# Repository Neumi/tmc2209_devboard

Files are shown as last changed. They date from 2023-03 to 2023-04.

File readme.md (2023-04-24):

# TMC2209 Development Board for Arduino Uno
A development board to test the Trinamic TMC2209 stepper motor controller on an Arduino Uno.

This board should cover all options and IOs that Trinamic provides for its TMC2209.

Facts:
 - All TMC2209 pins are connected to digital pins of the Arduino. 
 - XT30 power connector
 - voltage source selector Arduino VIN or XT30
 - TVS diodes on 5v and 28V lane of the TMC2209
 - different wiring schemes for the JST motor connector (because getting the right phases is not easy apparently!)
 - different current setting selectable with solder bridges (or custom resistor also possible)
 - motor voltage sensing via voltage divider on A0
 - reset button for Arudino + power LED

KICAD and production files for JLCPCB are also included. Code will follow. 
Production cost incl assembly is around 50€ for 5pcs. THT components not included.

Feedback is very welcome!

## Video:
LINK TO VIDEO (https://www.youtube.com/watch?v=-AFWAARrtoE)

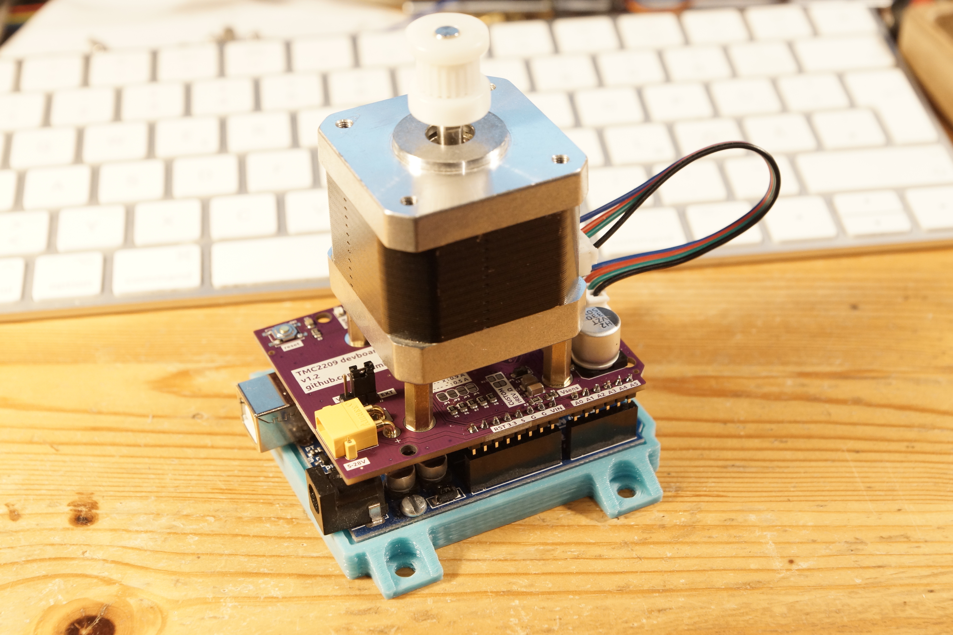
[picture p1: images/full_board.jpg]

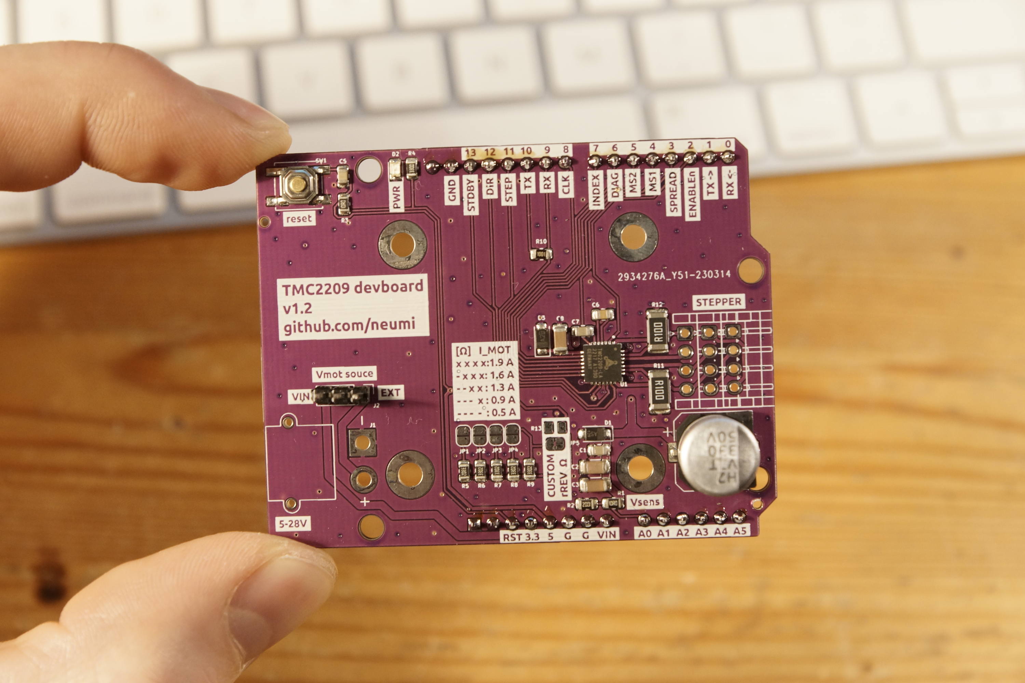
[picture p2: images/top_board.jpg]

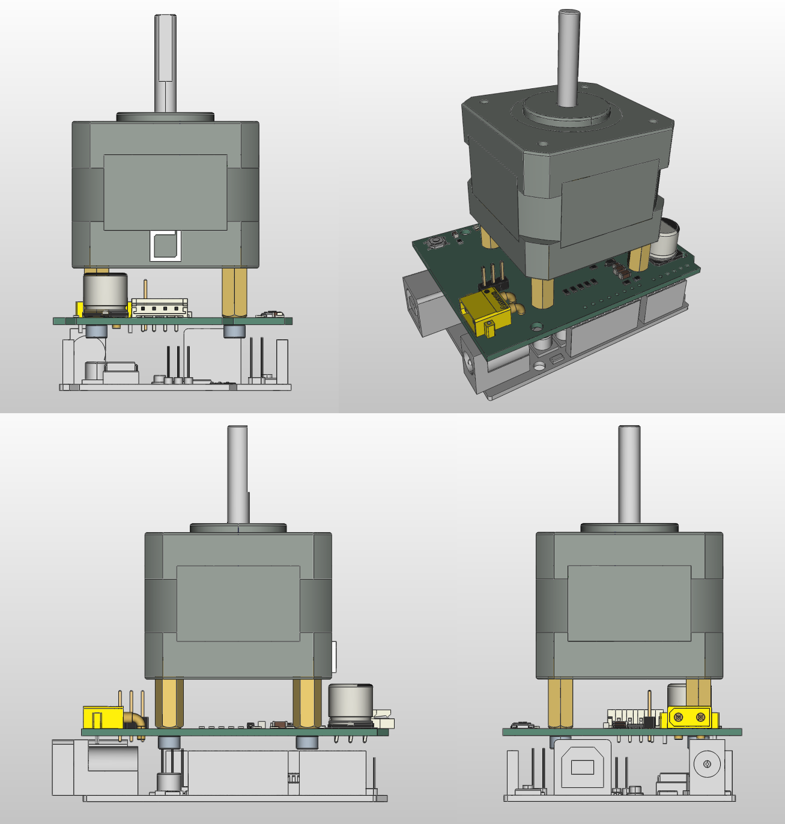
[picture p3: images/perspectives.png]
PCB assembly perspectives

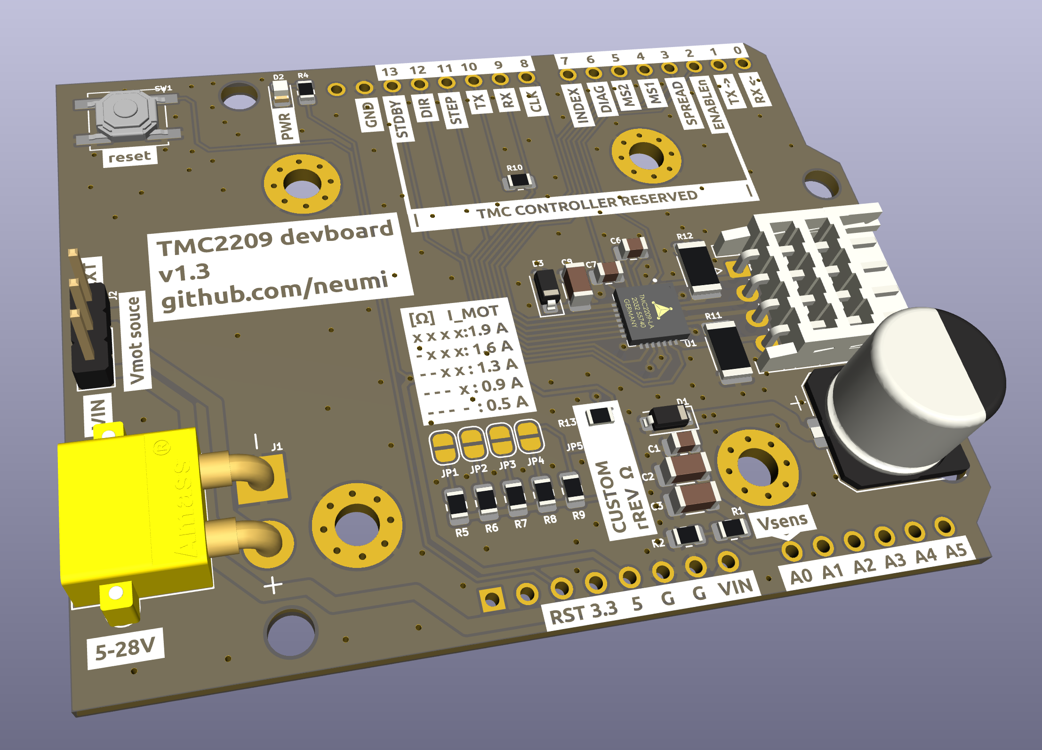
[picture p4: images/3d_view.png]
PCB 3d view

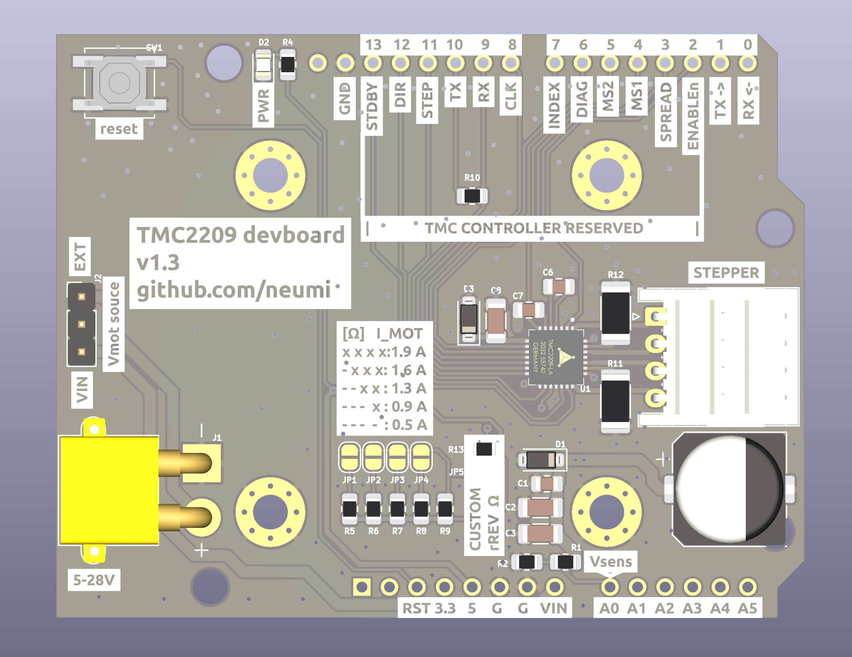
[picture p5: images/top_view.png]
top view

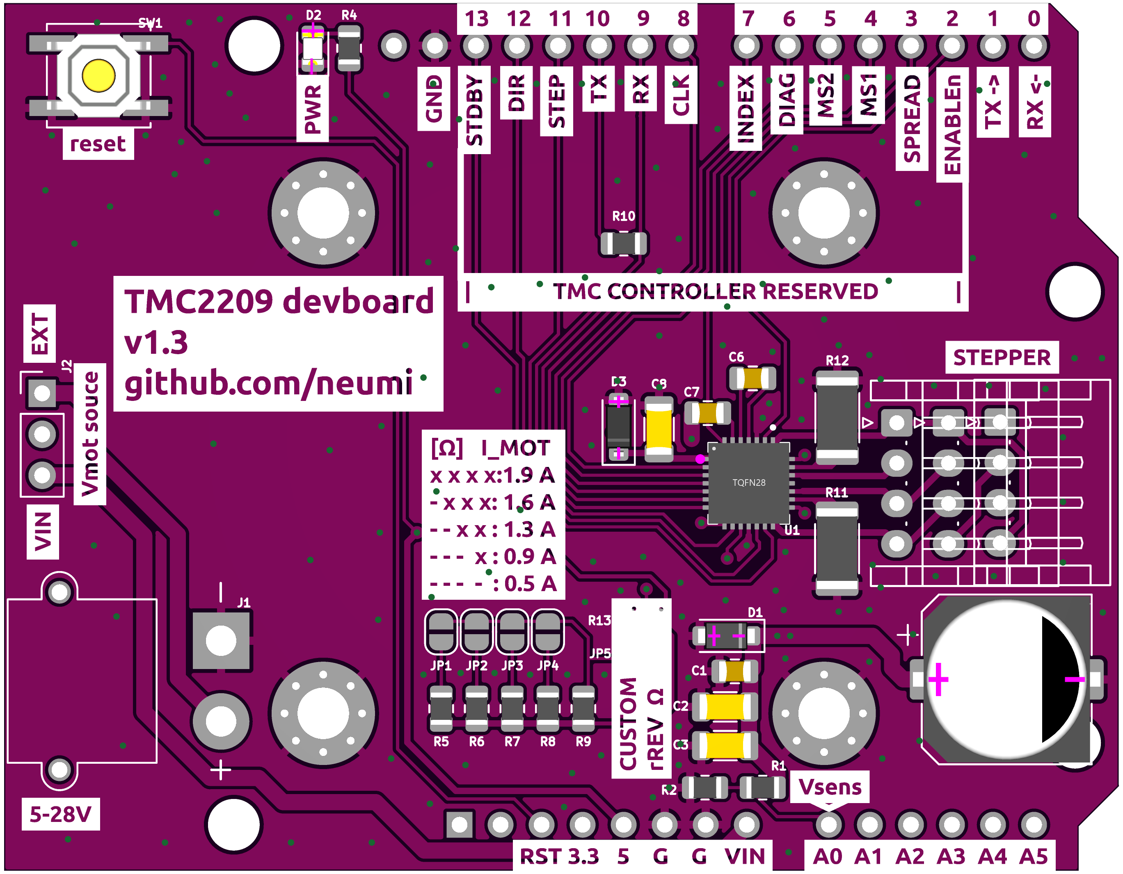
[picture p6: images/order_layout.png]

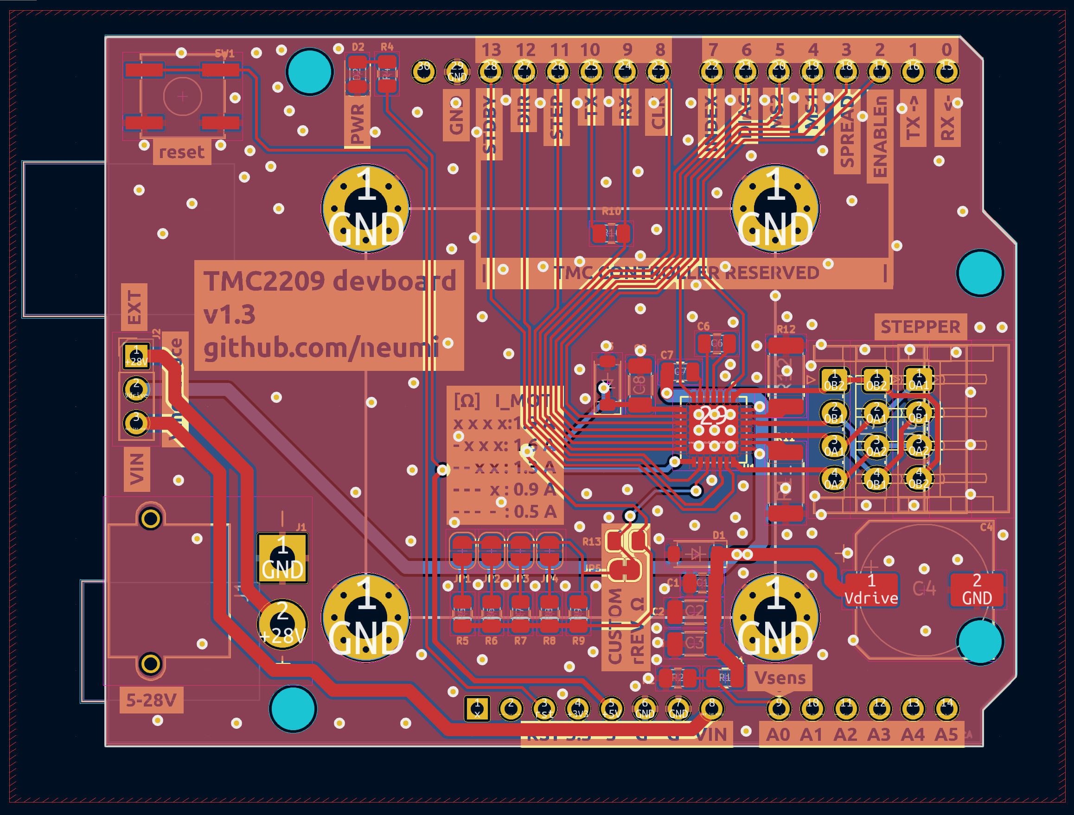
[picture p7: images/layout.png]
PCB layout


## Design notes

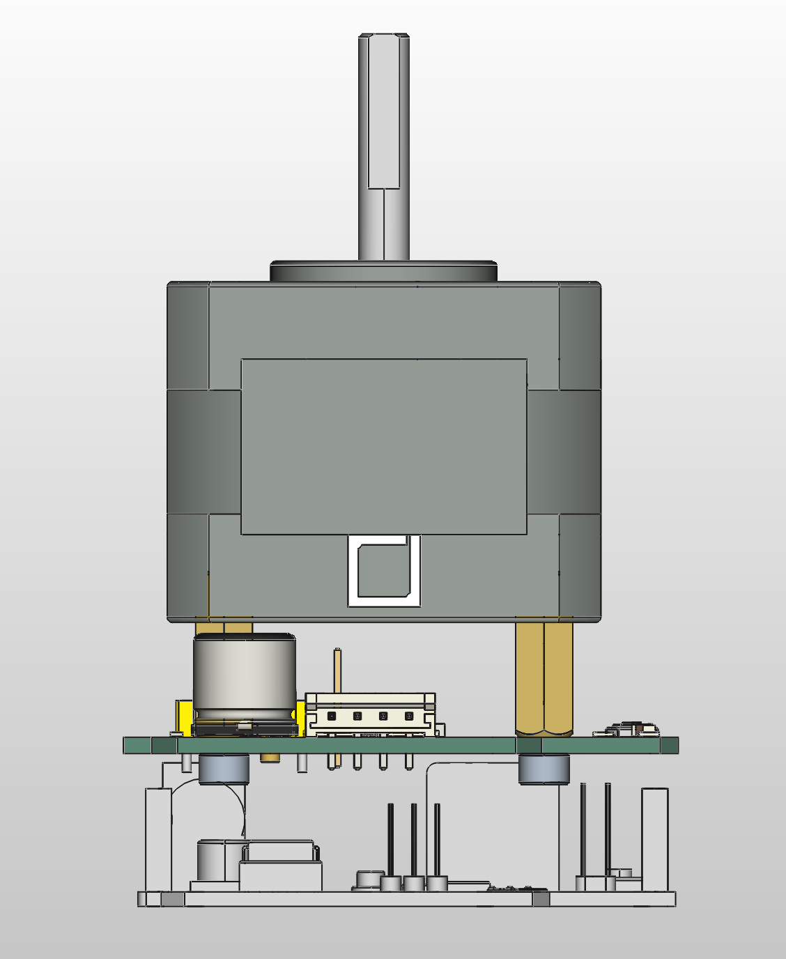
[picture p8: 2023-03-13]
images/back.png

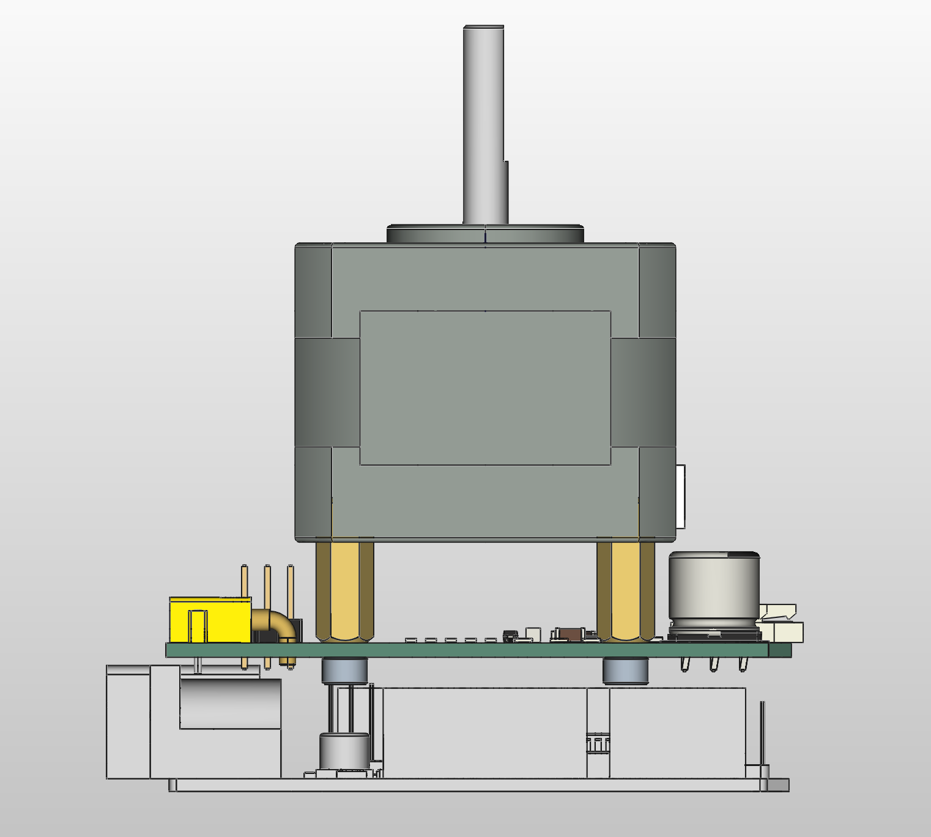
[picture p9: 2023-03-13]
images/side.png

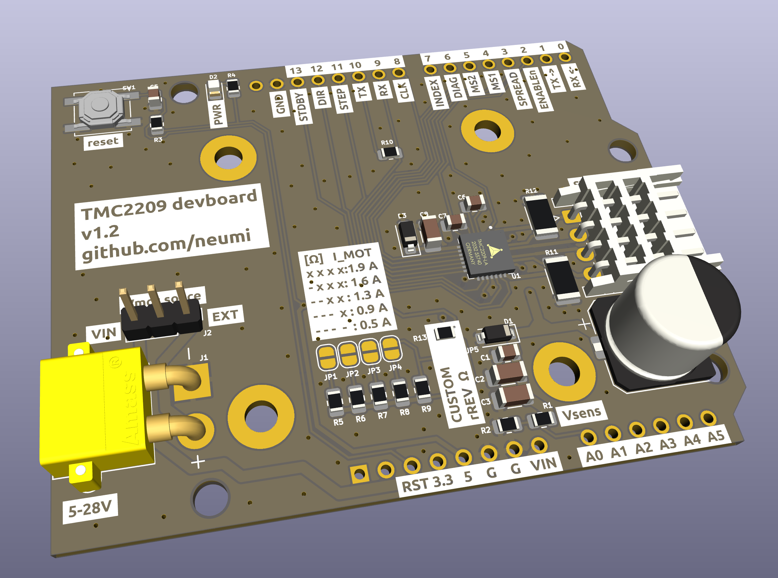
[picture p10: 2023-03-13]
images/3d _view.png

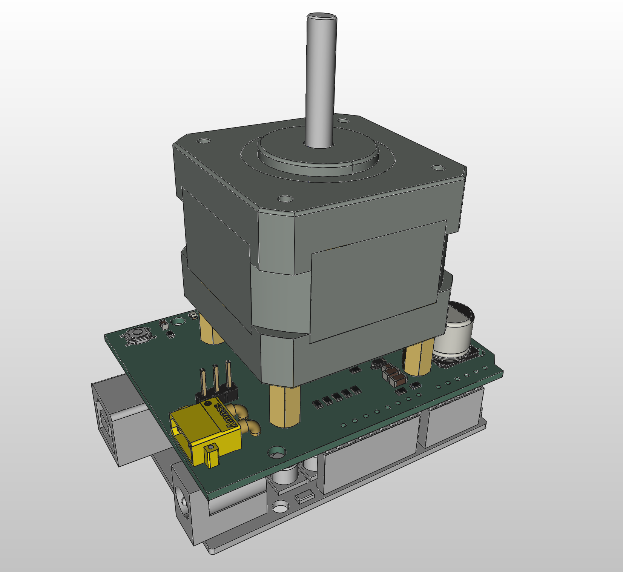
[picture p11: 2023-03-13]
images/diagonal.png

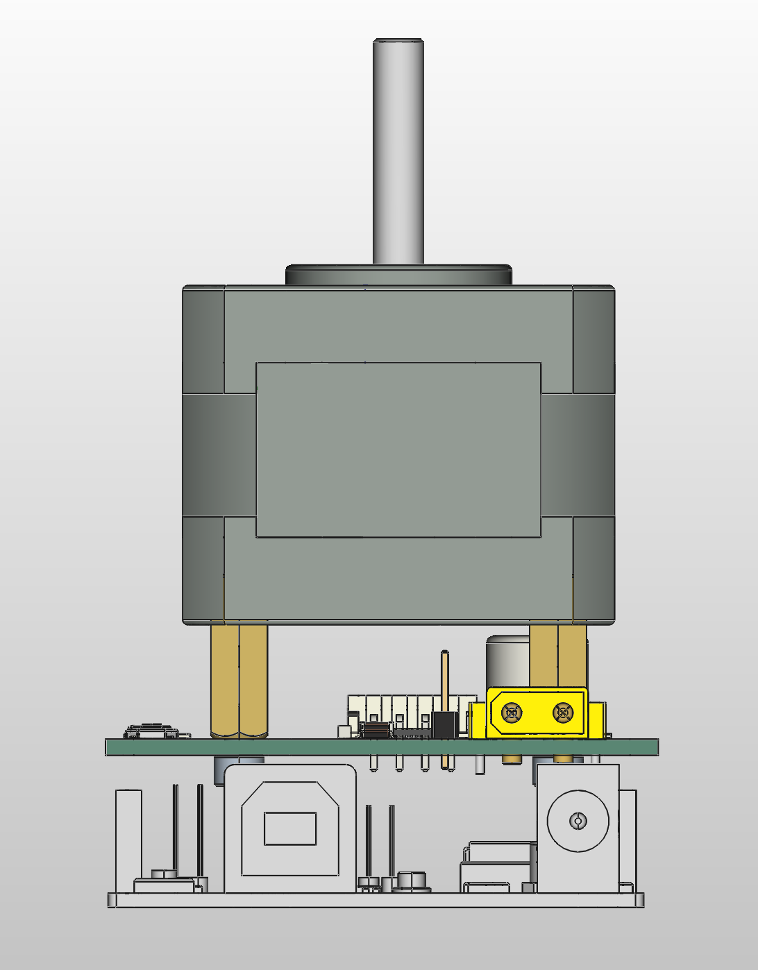
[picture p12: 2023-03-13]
images/front.png

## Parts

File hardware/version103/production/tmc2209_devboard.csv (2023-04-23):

Comment | Designator | Footprint | LCSC
C100nF | C1,C7 | Capacitor_SMD:C_0805_2012Metric | C49678
C10uF | C2 | Capacitor_SMD:C_1206_3216Metric | C13585
C4.7uF | C3 | Capacitor_SMD:C_1206_3216Metric | C29823
C_330uF | C4 | Capacitor_SMD:CP_Elec_10x10 | C249985
C22nF 50V | C6 | Capacitor_SMD:C_0805_2012Metric | C1729
C2.2-4.7uF ceramic | C8 | Capacitor_SMD:C_1206_3216Metric | C29823
D_TVS_30V | D1 | Diode_SMD:D_SOD-123 | C553410
LED | D2 | LED_SMD:LED_0805_2012Metric | C84256
D_TVS_5V | D3 | Diode_SMD:D_SOD-123 | C478011
Conn_01x03_Pin | J2 | Connector_PinHeader_2.54mm:PinHeader_1x03_P2.54mm_Vertical
motor_conn | J4,J5,J6 | Connector_JST:JST_EH_S4B-EH_1x04_P2.50mm_Horizontal
Jumper | JP1,JP2,JP3,JP4 | Jumper:SolderJumper-2_P1.3mm_Open_RoundedPad1.0x1.5mm
SolderJumper_2_Bridged | JP5 | Jumper:SolderJumper-2_P1.3mm_Bridged_RoundedPad1.0x1.5mm
R10k | R1 | Resistor_SMD:R_0805_2012Metric | C3016734
R1k | R10 | Resistor_SMD:R_0805_2012Metric | C17513
R100mOHM | R11,R12 | Resistor_SMD:R_2010_5025Metric | C175979
R2k | R2 | Resistor_SMD:R_0805_2012Metric | C17604
R330 | R4 | Resistor_SMD:R_0805_2012Metric | C17630
R33k | R5,R6,R7,R8,R9,R13 | Resistor_SMD:R_0805_2012Metric | C17633
SW_Push | SW1 | Button_Switch_SMD:SW_Push_1P1T_NO_CK_KSC6xxJ | C318884
TMC2209-LA | U1 | components:QFN50P500X500X90-29N | C465949

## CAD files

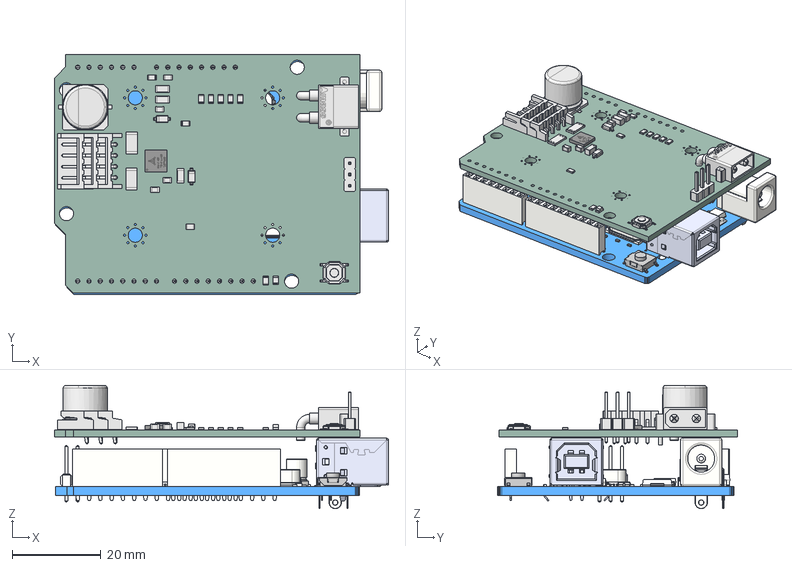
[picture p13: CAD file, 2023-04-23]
hardware/version103/tmc2209_devboard_assembly_103.FCStd
75.4 x 54.1 x 27.8 mm
PCB
pcb
16MHz Crystal
16MHz Crystal001
DC_Jack
heder female 8
heder female 009
heder female 10
red buttom
header male 2
header male 003
header male 004
heder female 6
47uF 27v cap
47uF 27v cap001
Atmega328p-AU
LM358
CH340G
LM1117
transistor SOC
transistor SOC001
diode
R1
0603 Package
0603 Package001
0603 Package002
0603 Package003
0603 Package004
0603 Package005
0603 Package006
0603 Package007
0603 Package008
0603 Package009
0603 Package010
0603 Package011
0603 Package012
0603 Package013
0603 Package014
0603 Package015
0603 Package016
0603 Package017
0603 Package018
0603 Package019
0603 Package020
0603 Package021

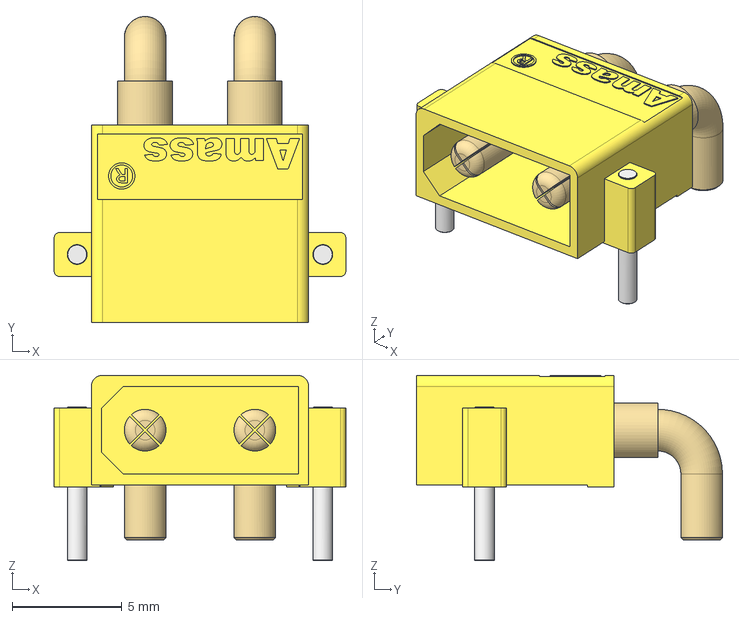
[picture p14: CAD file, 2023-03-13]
hardware/version103/3d_files/XT30PW-M_pcb.stp
13.3 x 13.9 x 8.45 mm

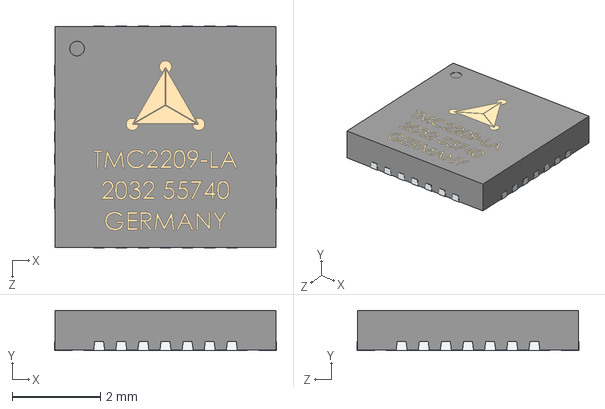
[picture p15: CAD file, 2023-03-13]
hardware/version103/3d_files/TMC2209.STEP
5.02 x 0.911 x 5.02 mm

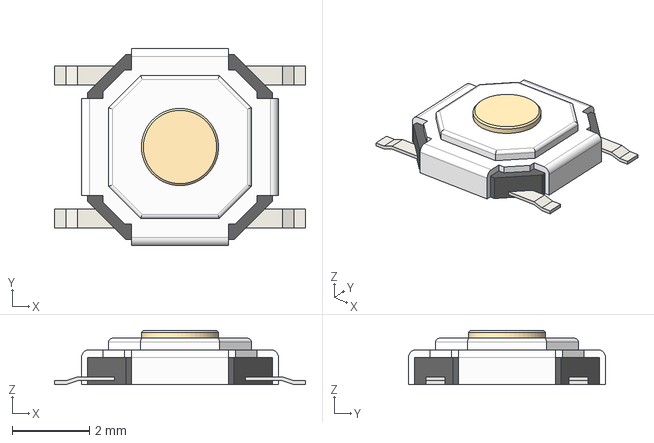
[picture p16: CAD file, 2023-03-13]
hardware/version103/3d_files/TS-1187A.step
6.50 x 5.10 x 1.40 mm

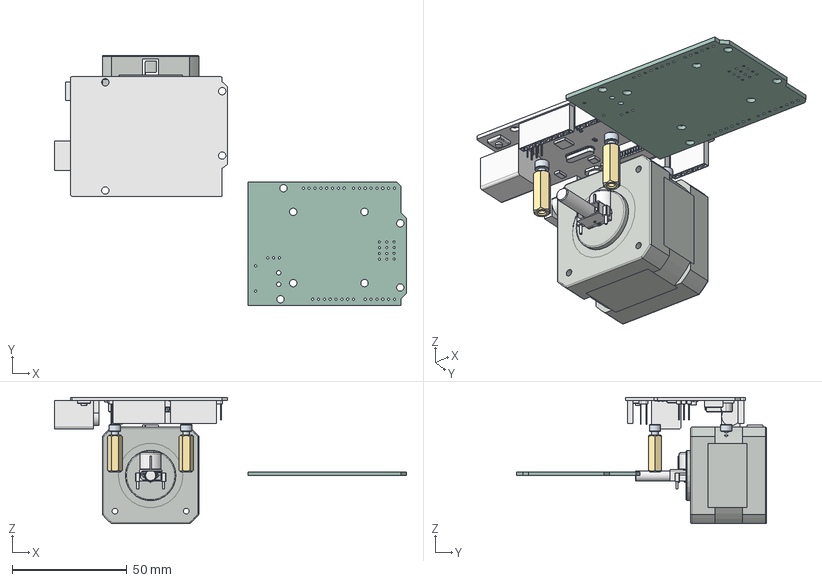
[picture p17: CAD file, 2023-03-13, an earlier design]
hardware/version102/full_assembly.FCStd
153.1 x 108.7 x 55.0 mm
standoff1
standoff2
standoff3
standoff4
M3x5mm1
M3x5mm2
M3x5mm3
M3x5mm4
front
back
connector
case
bearing1
bearing2
shaft
PCB
ARDUINO UNO R3 Step

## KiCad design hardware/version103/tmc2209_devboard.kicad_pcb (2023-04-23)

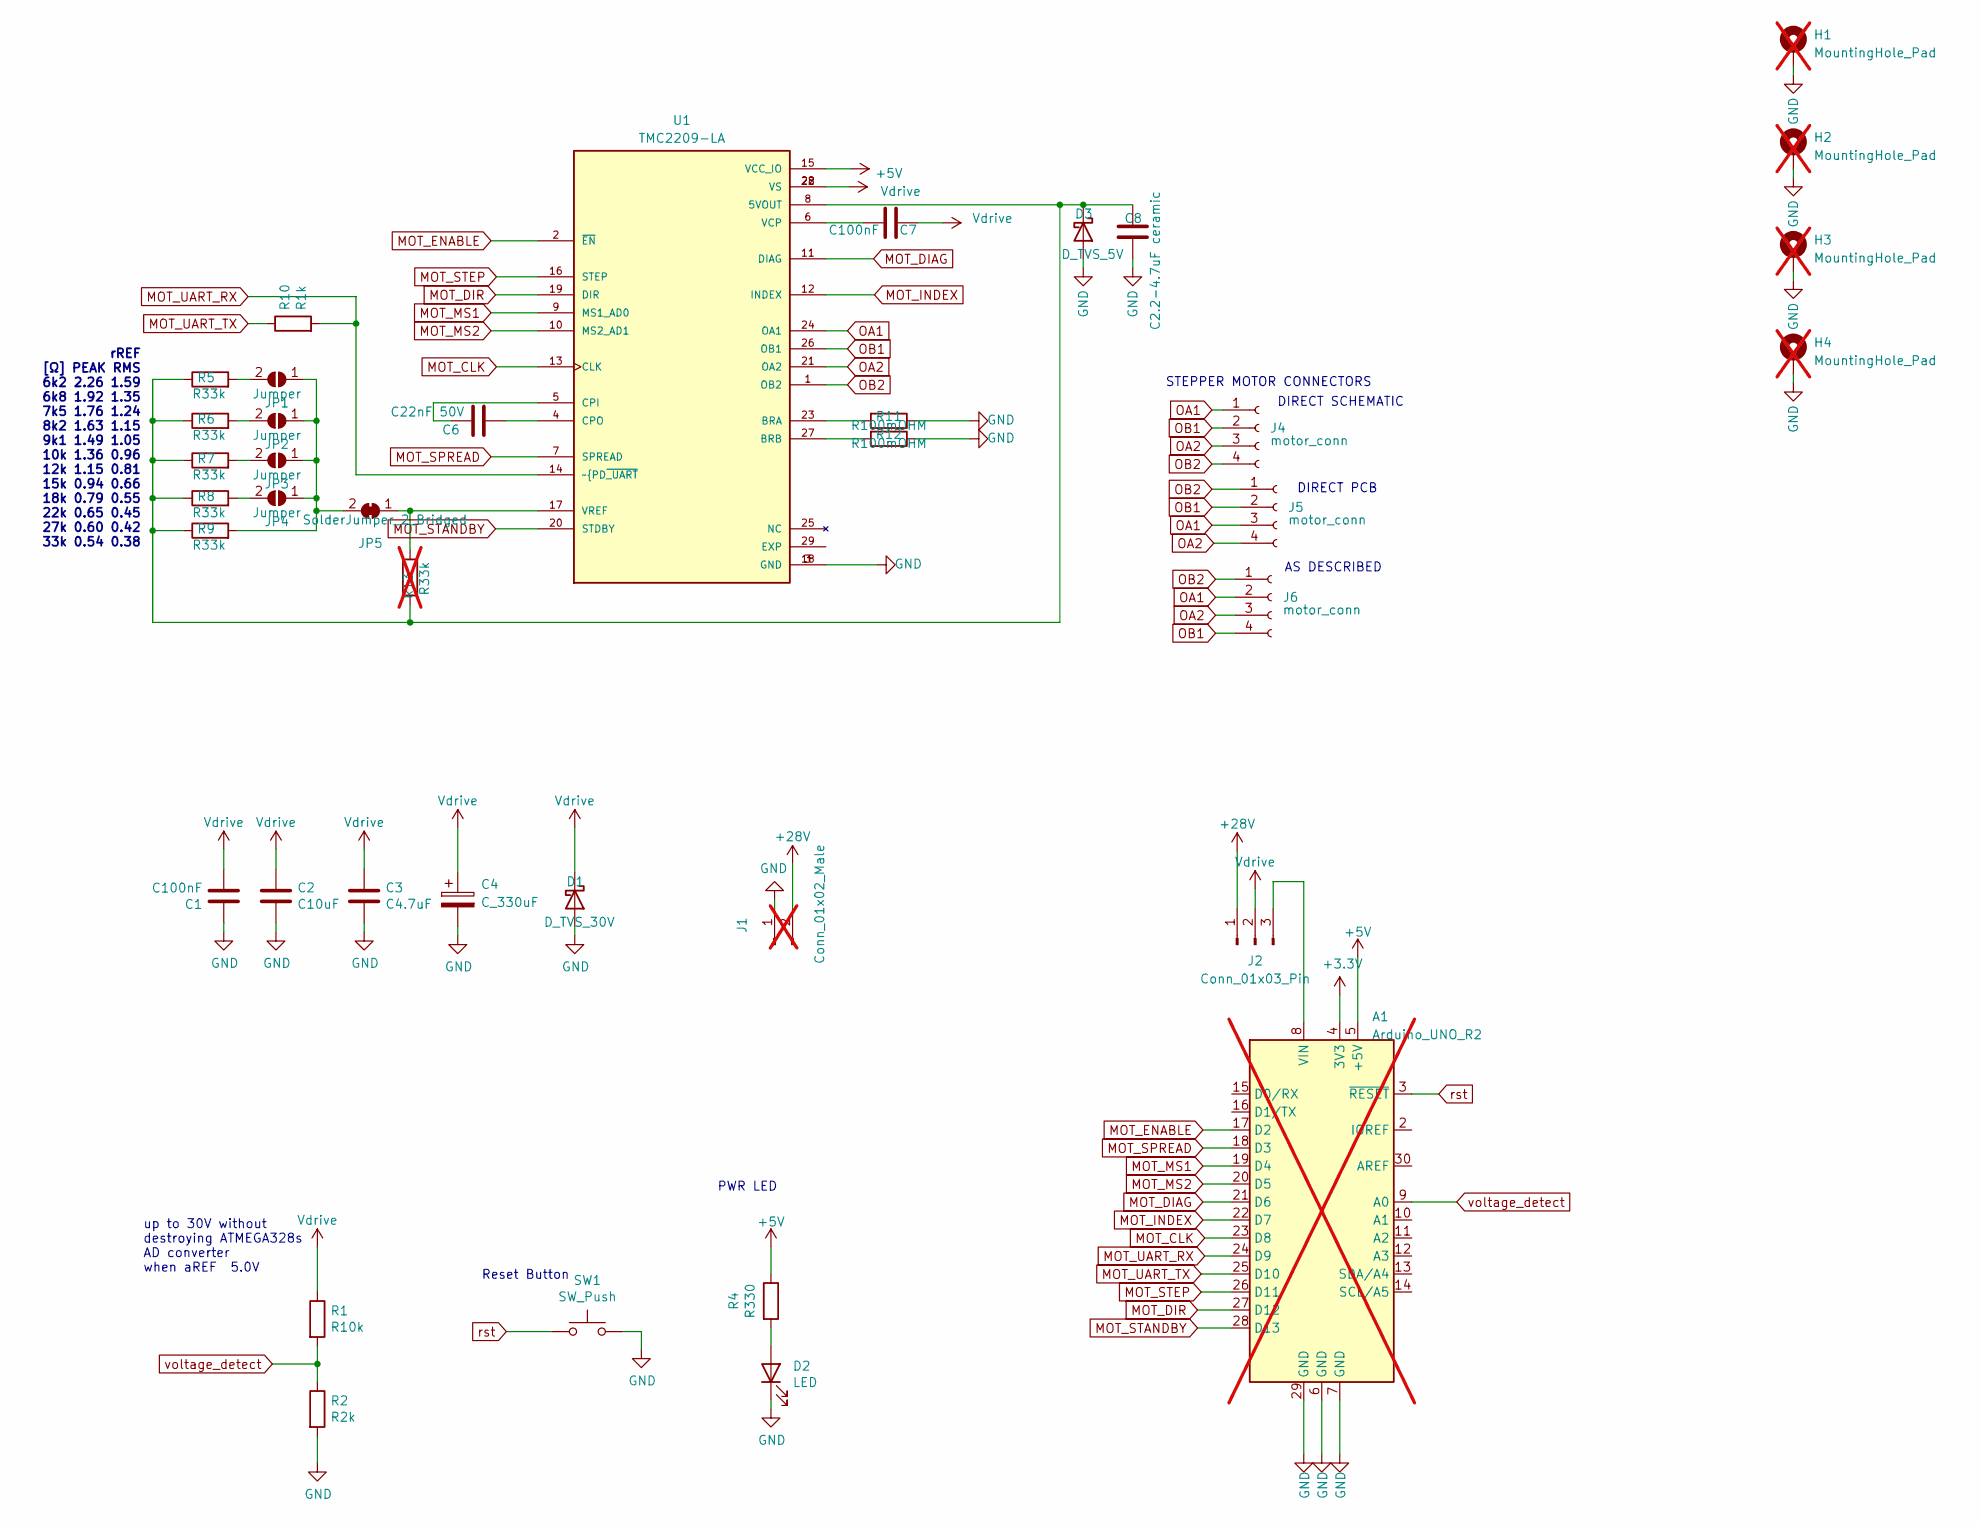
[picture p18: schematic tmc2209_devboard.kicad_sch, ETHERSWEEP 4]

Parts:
A1: Arduino_UNO_R2; Arduino_UNO_R2_WithMountingHoles; not fitted
C1, C7: C100nF; C_0805_2012Metric; LCSC C49678
C2: C10uF; C_1206_3216Metric; LCSC C13585
C3: C4.7uF; C_1206_3216Metric; LCSC C29823
C4: C_330uF; CP_Elec_10x10; LCSC C249985
C6: C22nF 50V; C_0805_2012Metric; LCSC C1729
C8: C2.2-4.7uF ceramic; C_1206_3216Metric; LCSC C29823
D1: D_TVS_30V; D_SOD-123; LCSC C553410
D2: LED; LED_0805_2012Metric; LCSC C84256
D3: D_TVS_5V; D_SOD-123; LCSC C478011
H1, H2, H3, H4: MountingHole_Pad; MountingHole_3.2mm_M3_Pad_Via; not fitted
J1: Conn_01x02_Male; AMASS_XT30PW-M_1x02_P2.50mm_Horizontal; LCSC C431092; not fitted
J2: Conn_01x03_Pin; PinHeader_1x03_P2.54mm_Vertical
J4, J5, J6: motor_conn; JST_EH_S4B-EH_1x04_P2.50mm_Horizontal
JP1, JP2, JP3, JP4: Jumper; SolderJumper-2_P1.3mm_Open_RoundedPad1.0x1.5mm
JP5: SolderJumper_2_Bridged; SolderJumper-2_P1.3mm_Bridged_RoundedPad1.0x1.5mm
R1: R10k; R_0805_2012Metric; LCSC C3016734
R2: R2k; R_0805_2012Metric; LCSC C17604
R4: R330; R_0805_2012Metric; LCSC C17630
R5, R6, R7, R8, R9: R33k; R_0805_2012Metric; LCSC C17633
R10: R1k; R_0805_2012Metric; LCSC C17513
R11, R12: R100mOHM; R_2010_5025Metric; LCSC C175979
R13: R33k; R_0805_2012Metric; LCSC C17633; not fitted
SW1: SW_Push; SW_Push_1P1T_NO_CK_KSC6xxJ; LCSC C318884
U1: TMC2209-LA; QFN50P500X500X90-29N; PARTREV 1.08; LCSC C465949

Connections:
+3V3: A1.4 (3V3)
+5V: A1.5 (+5V), R4.1, U1.15 (VCC_IO)
+28V: J1.2, J2.1
GND: A1.6 (GND), A1.7 (GND), A1.29 (GND), C1.1, C2.2, C3.2, C4.2, C8.2, D1.2 (A), D2.1 (K), D3.2 (A), H1.1, H2.1, H3.1, H4.1, J1.1, R2.2, R11.1, R12.1, SW1.2, U1.3 (GND), U1.18 (GND)
MOT_CLK: A1.23 (D8), U1.13 (CLK)
MOT_DIAG: A1.21 (D6), U1.11 (DIAG)
MOT_DIR: A1.27 (D12), U1.19 (DIR)
MOT_ENABLE: A1.17 (D2), U1.2 (~EN)
MOT_INDEX: A1.22 (D7), U1.12 (INDEX)
MOT_MS1: A1.19 (D4), U1.9 (MS1_AD0)
MOT_MS2: A1.20 (D5), U1.10 (MS2_AD1)
MOT_SPREAD: A1.18 (D3), U1.7 (SPREAD)
MOT_STANDBY: A1.28 (D13), U1.20 (STDBY)
MOT_STEP: A1.26 (D11), U1.16 (STEP)
MOT_UART_RX: A1.24 (D9), R10.2, U1.14 (~PD~{_UART)
MOT_UART_TX: A1.25 (D10), R10.1
unnamed: A1.8 (VIN), J2.3
unnamed: D2.2 (A), R4.2
unnamed: C8.1, D3.1 (K), R5.1, R6.1, R7.1, R8.1, R9.1, R13.1, U1.8 (5VOUT)
unnamed: JP1.1 (A), JP2.1 (A), JP3.1 (A), JP4.1 (A), JP5.2 (B), R9.2
unnamed: JP1.2 (B), R5.2
unnamed: JP2.2 (B), R6.2
unnamed: JP3.2 (B), R7.2
unnamed: JP4.2 (B), R8.2
unnamed: JP5.1 (A), R13.2, U1.17 (VREF)
unnamed: R11.2, U1.23 (BRA)
unnamed: R12.2, U1.27 (BRB)
unnamed: C6.1, U1.5 (CPI)
unnamed: C6.2, U1.4 (CPO)
unnamed: C7.1, U1.6 (VCP)
OA1: J4.1, J5.3, J6.2, U1.24 (OA1)
OA2: J4.3, J5.4, J6.3, U1.21 (OA2)
OB1: J4.2, J5.2, J6.4, U1.26 (OB1)
OB2: J4.4, J5.1, J6.1, U1.1 (OB2)
Vdrive: C1.2, C2.1, C3.1, C4.1, C7.2, D1.1 (K), J2.2, R1.1, U1.22 (VS), U1.28 (VS)
rst: A1.3 (~RESET), SW1.1
voltage_detect: A1.9 (A0), R1.2, R2.1

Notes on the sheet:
STEPPER MOTOR CONNECTORS
DIRECT SCHEMATIC
AS DESCRIBED
PWR LED
up to 30V without destroying ATMEGA328s AD converter when aREF 5.0V
rREF [Ω] PEAK RMS 6k2 2.26 1.59 6k8 1.92 1.35 7k5 1.76 1.24 8k2 1.63 1.15 9k1 1.49 1.05 10k 1.36 0.96 12k 1.15 0.81 15k 0.94 0.66 18k 0.79 0.55 22k 0.65 0.45 27k 0.60 0.42 33k 0.54 0.38
DIRECT PCB
Reset Button

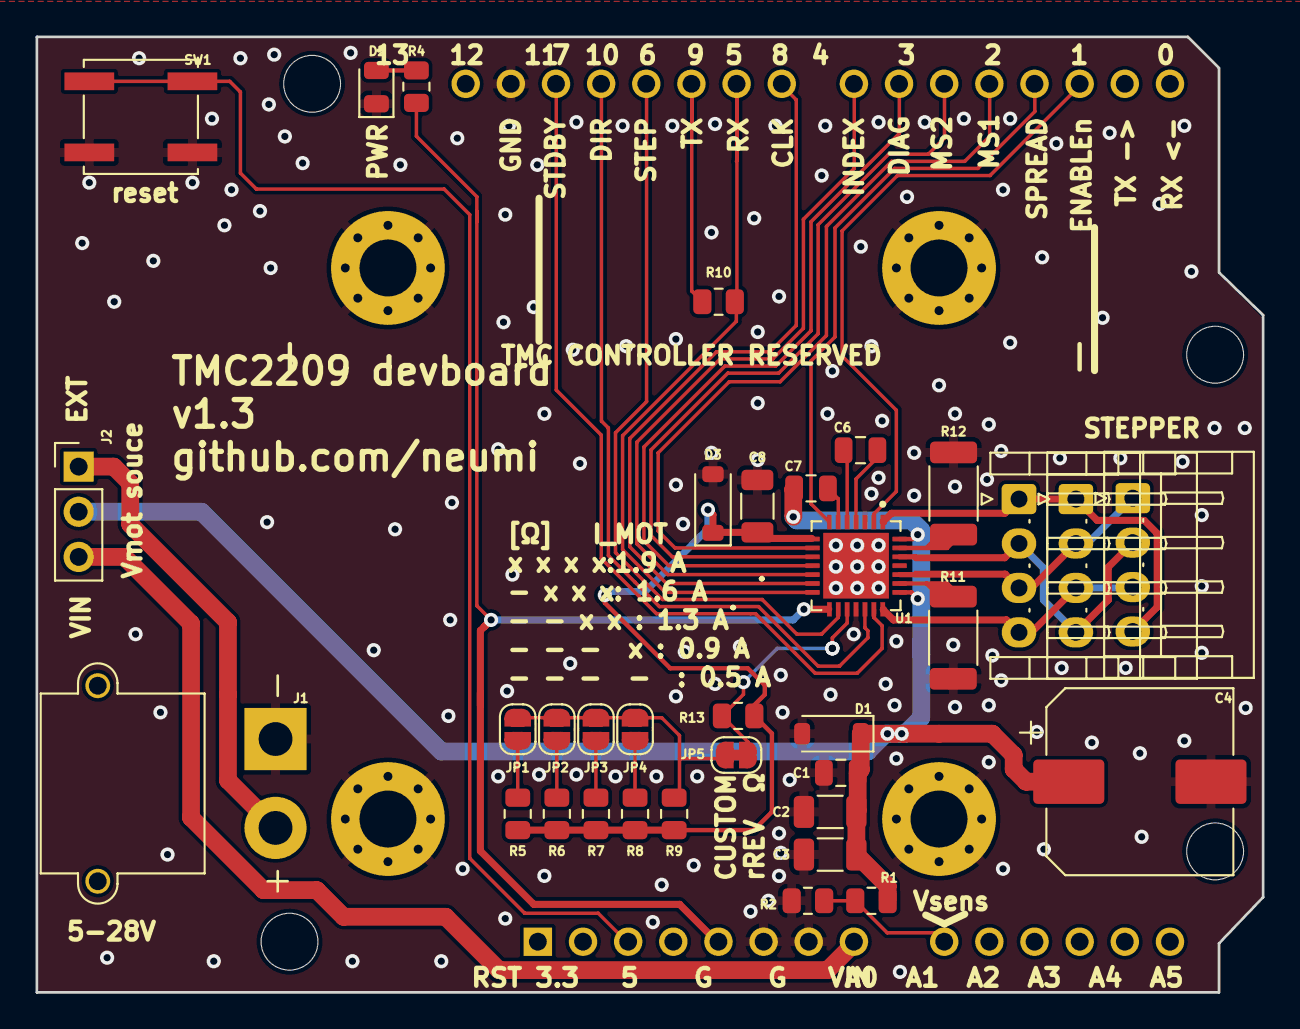
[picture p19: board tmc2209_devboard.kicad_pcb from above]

Board: 2 copper layers, 69.0 x 53.8 mm, 39 parts (1 on the bottom side), 36 nets.

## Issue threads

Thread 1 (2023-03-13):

add nema17 screw spacing

Neumi, 2023-03-13:
It should be possible to connect a nema17 motor to the PCB with four m3 screws in a 31x31mm spacing.

Neumi, 2023-03-13:
solved in #2 b94a8fa35f1b20be82e50deae4e53ce20a47b1a0

Closed 2023-03-13.

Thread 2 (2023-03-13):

Motor power source incorrect

Neumi, 2023-03-13:
VIN and EXT power labels are incorrect (switched)

Neumi, 2023-03-13:
solve in #2 b94a8fa35f1b20be82e50deae4e53ce20a47b1a0

Closed 2023-03-13.

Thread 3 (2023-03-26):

R3 wrong value for JLC parts

Neumi, 2023-03-26:
Should be 10k not 10r

Neumi, 2023-03-29:
solved in version 103. resistor and capacitor are not needed as they are already present on all Arduino boards. On older versions, they can just be desoldered.

Closed 2023-03-29.

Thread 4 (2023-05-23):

Error in format of CPL file

RDDyer, 2023-05-23:
The csv file that JLCPCB uses for the Assembly process appears to have an error in it. When I submitted the Production ZIP file I got an error because they want the last two columns of the file to be Layer and then Rotation. The existing file has them switched. It was an easy edit, but since this was my first time ordering an Assembly, it confused me for a little while.

Also huge thanks to you for creating this project. As you said the price for 5 assembled boards is just over $50 with 1/3 of that being shipping. The other problem was that they were out of the current sense resistors, so I'll order them from DigiKey and solder them by hand.

Really excited to try them out.

Neumi, 2023-05-23:
Thanks!
I tried to reproduce the error. The files seem right to me. I used version 103 with these files:
Gerber:
https://github.com/Neumi/tmc2209_devboard/blob/master/hardware/version103/production.zip
BOM:
https://github.com/Neumi/tmc2209_devboard/blob/master/hardware/version103/production/tmc2209_devboard.csv
Position:
https://github.com/Neumi/tmc2209_devboard/blob/master/hardware/version103/production/tmc2209_devboard-top-pos.csv

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

Let me know if you need any help. If the boards arrive, I would love to see a picture of them in action!

RDDyer, 2023-05-23:
Thank you for checking. As this was my first attempt at using JLCPCB I wasn't confident of my process. Now I'm not sure which file I was using. I did check the file myself, and the columns were reversed in the file, just as the error said. I hope I didn't use the wrong version. I'm pretty sure I was using v103. I hope I didn't screw up my order. Yikes!!

 The PCBs are 29% finished at this time. I ordered black solder mask with white silkscreen. I'll send you a pic when they arrive, but I'm not sure how soon I'll have them actually running. I'm headed out of the country for almost all of June, just shortly after the boards arrive. If I don't have any trouble using the sample code, they'll probably come right up.

 Thanks again for providing this board to the community. I haven't seen many 2209 boards out there, especially with an UNO shield form factor.

----------------------------------------
 From: "Neumi" ***@***.***>
Sent: Tuesday, May 23, 2023 1:56 AM
To: "Neumi/tmc2209_devboard" ***@***.***>
Cc: "RDDyer" ***@***.***>, "Author" ***@***.***>
Subject: Re: [Neumi/tmc2209_devboard] Error in format of CPL file (Issue #4)

Thanks!
I tried to reproduce the error. The files seem right to me. I used version 103 with these files:
Gerber:
https://github.com/Neumi/tmc2209_devboard/blob/master/hardware/version103/production.zip
BOM:
https://github.com/Neumi/tmc2209_devboard/blob/master/hardware/version103/production/tmc2209_devboard.csv
Position:
https://github.com/Neumi/tmc2209_devboard/blob/master/hardware/version103/production/tmc2209_devboard-top-pos.csv

Let me know if you need any help. If the boards arrive, I would love to see a picture of them in action!


Reply to this email directly, view it on GitHub, or unsubscribe.
You are receiving this because you authored the thread.Message ID: ***@***.***>

Neumi, 2023-06-07:
This should not be such a big problem. The parts I changed were the capacitor and resistor for the reset button and the one part number of the Vsens resistor (was 10 ohm accidentally changed to 10k). Therefore JLC would have complained that they cant place the parts I guess :D Let me know if you made progress! :)

Closed 2023-06-07.

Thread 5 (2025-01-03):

Please add clarification of process to make these boards for PCB n00bs

etotheipi, 2025-01-03:
I spend a lot of time dealing with NEMA17 steppers and TMC2209s and this project looks like it would really simplify my life.  However, I have zero experience with PCB design or getting PCBs made.  I blindly loaded the production.zip file into JLCPCB and it appears to have read it correctly, but there's so many options and I have no clue what any are, and I don't know if I'll actually end up with usable boards when they arrive.

If I'm in over my head, and one needs PCB experience to actually make this work, can you please state that somewhere?   If you think it's doable to blindly load the zip file into JLCPCB and get usable boards, could you also state that, along with any recommendations for options to select?  I'm resisting the urge to just accept the default everything and order the boards with a few prayers as I enter my CC info :sweat_smile:

Neumi, 2025-01-03:
It was designed to test firmware for the TMC22xx series chips. It could also be used as a stepper shield of course. If it simplifies your life, I don't know. Maybe. As this is a hardware development project, I usually assume that users are familiar with PCB design and the associated ordering process.
The ordering process changes quite often. Describing the exact ordering process might not be useful for long. But the standard settings are ok most of the time. If you need parts assembled (and not the raw PCB without components) you need to upload the CPL and BOM fies as well. The files in the repo are the ones I used for the production of my boards. Back then, it worked.

Follow the steps in the video after this timestamp: https://www.youtube.com/watch?v=v9FglN80EMM&t=515
If the SMT assembly process does not show any parts missing, you should be good to go.

The standard parameters for the PCB manufacturing in JLC are ok for the board (and also the cheapest).

etotheipi, 2025-01-03:
Thanks for the response.  I know it's a dev project, but I'm just a hobbyist tinkerer, mostly into building simple machines for fun and with my kids.  The kind of stuff that never needs to leave a breadboard.  And every time I want to play with a stepper, I grumble at the thought of the noise from an A4988 or DRV8825, and grumble more at the tedium of trying to setup a TMC2209 with UART control.  It's a struggle every time even though I technically know what I'm doing.  I love the compactness and simplicity of what you've designed.

Thanks for the link, that's exactly what I needed.   I found this project via github, not via your Youtube channel, so I didn't even know there were videos about it.

I will follow the instructions and take a shot at it.  It'll be worth wasting a few dollars if it doesn't work, and possibly encourage me to learn more about PCB design if it needs some manual tweaking.  Thanks so much!

Closed 2025-01-03.

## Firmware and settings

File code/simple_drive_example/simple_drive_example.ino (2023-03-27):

#include <TMCStepper.h> // TMCstepper - https://github.com/teemuatlut/TMCStepper
#include <SoftwareSerial.h> // Software serial - https://www.arduino.cc/en/Reference/softwareSerial

#define MS1_PIN  4
#define MS2_PIN  5
#define EN_PIN 2
#define SW_TX 10
#define SW_RX 9

#define DRIVER_ADDRESS 0x00 // TMC2209 driver address when MS1 LOW and MS2 LOW
#define R_SENSE 0.1f // TMC2209 Devboard v1.2 by Neumi uses 100mOhm
bool dir = false;

SoftwareSerial SoftSerial(SW_RX, SW_TX);
TMC2209Stepper TMCdriverX(&SoftSerial, R_SENSE, DRIVER_ADDRESS);

void setup() {
  SoftSerial.begin(115200);
  TMCdriverX.beginSerial(115200);

  pinMode(EN_PIN, OUTPUT);
  pinMode(MS2_PIN, OUTPUT);
  pinMode(MS1_PIN, OUTPUT);

  digitalWrite(EN_PIN, LOW);
  digitalWrite(MS1_PIN, LOW);
  digitalWrite(MS2_PIN, LOW);


  TMCdriverX.begin();
  TMCdriverX.toff(5);
  TMCdriverX.rms_current(500); // motor current in mA
  TMCdriverX.microsteps(64); // microsteps in 1/x
  TMCdriverX.en_spreadCycle(false);
  TMCdriverX.pwm_autoscale(true); // needed for stealthChop
  TMCdriverX.VACTUAL(12000); // motor speed
  TMCdriverX.step();
}

void loop() {
  delay(100);
  dir = !dir;
  TMCdriverX.shaft(dir);

  delay(500);
  TMCdriverX.VACTUAL(50000);

  delay(500);
  dir = !dir;
  TMCdriverX.shaft(dir);
  delay(500);

  TMCdriverX.VACTUAL(12000);
  delay(200);
  for (int i = 0; i <= 20; i++) {
    dir = !dir;
    TMCdriverX.shaft(dir);
    delay(50);
  }
}

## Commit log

2023-03-13 initial commit. version 1.0 production ready
    [TMC2209.STEP, TS-1187A.step, XT30PW-M_pcb.stp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]
2023-03-13 added version 102, added nema17 mount and fixed switched vin text
    [TMC2209.STEP, TS-1187A.step, XT30PW-M_pcb.stp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]
2023-03-13 fixed order files and added images
    [tmc2209_devboard-B_Cu.gbr, tmc2209_devboard-B_Mask.gbr, tmc2209_devboard-B_Paste.gbr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]
2023-03-13 added 3d files and perspective renderings
    [full_assembly.FCStd]
2023-03-26 minor changed for version 1.3. Changed component number for JLC parts for R3 (was wrong) relates #3
    [tmc2209_devboard.kicad_pcb, tmc2209_devboard.kicad_sch]
2023-03-26 added HW version 1.3
    [TMC2209.STEP, TS-1187A.step, XT30PW-M_pcb.stp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]
2023-03-26 Update readme.md
    added photos of finished 1.2 board
2023-03-28 Create FUNDING.yml
    added sponsoring button
2023-03-29 changed motor power source connector and elec cap for lower nema17 placement. Added production files for 103
    [tmc2209_devboard-B_Cu.gbr, tmc2209_devboard-B_Mask.gbr, tmc2209_devboard-B_Paste.gbr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]
2023-03-29 added gnd connection to motor mounts, added DNP for static PCB footprints
    [tmc2209_devboard.kicad_pcb, tmc2209_devboard.kicad_sch]
2023-04-23 minor design changes, added produciton files for version 103
    [tmc2209_devboard-B_Cu.gbr, tmc2209_devboard-B_Mask.gbr, tmc2209_devboard-B_Paste.gbr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]
